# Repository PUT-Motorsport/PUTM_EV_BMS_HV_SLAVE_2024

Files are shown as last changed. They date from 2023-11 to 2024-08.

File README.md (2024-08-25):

# PUTM_EV_BMS_HV_SLAVE_2024
Accumulator Managment System (High Voltage Battery Managment System)

## Overview
The AMS system consists of two main parts, the master and multiple slaves.
<p align="center">
  
</p>
The apparatus is responsible for the managment of the battery as a whole, determining it's states like: state of charge or unsafe state plausibility. It also supervises the turning on and off of the hv bus.

## Slave
The AMS Slave is a subsidiary system responsible for measuring all the cell voltages and strategically placed temperatures on one stack.
<p align="center"> 
  
</p>

### Hardware 
The AMS Slave is powered by LTC6811, a powerful, new gen IC capable of measuring of up to 12 cell simultaneously and up to 5 auxilary readings. One slave features 2 of such IC for a total of 20 cell and 10 temperature measurements. All Slaves are connected in chain configuration allowing for a quick data dump from all slaves in series. For interfacing the LTC6811 uses isoSPI, a special SPI/Ethernet like protocol, which features amazing noise immunity due to usage of a twisted differential pair. All of that on a custom 4 layer board. The AMS slave boasts a lot smaller (106mm x 50mm) size compared to it's predecessor allowing for a lot more versatile usage and making one cell stack far more compact. 

<p align="center"> 
  
</p>

### The research and development work was carried out was a part of the Student Scientific Clubs Create Innovations (SKNTI) program. [Ministry of Science and Higher Education](https://www.gov.pl/web/nauka)
baner-sknti

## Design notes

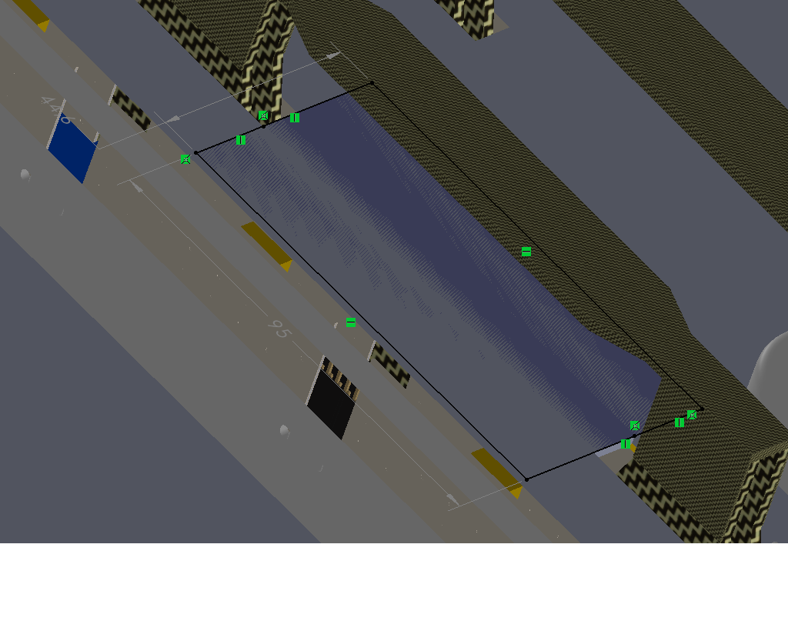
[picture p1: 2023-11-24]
hardware/images/wymiary v1.png

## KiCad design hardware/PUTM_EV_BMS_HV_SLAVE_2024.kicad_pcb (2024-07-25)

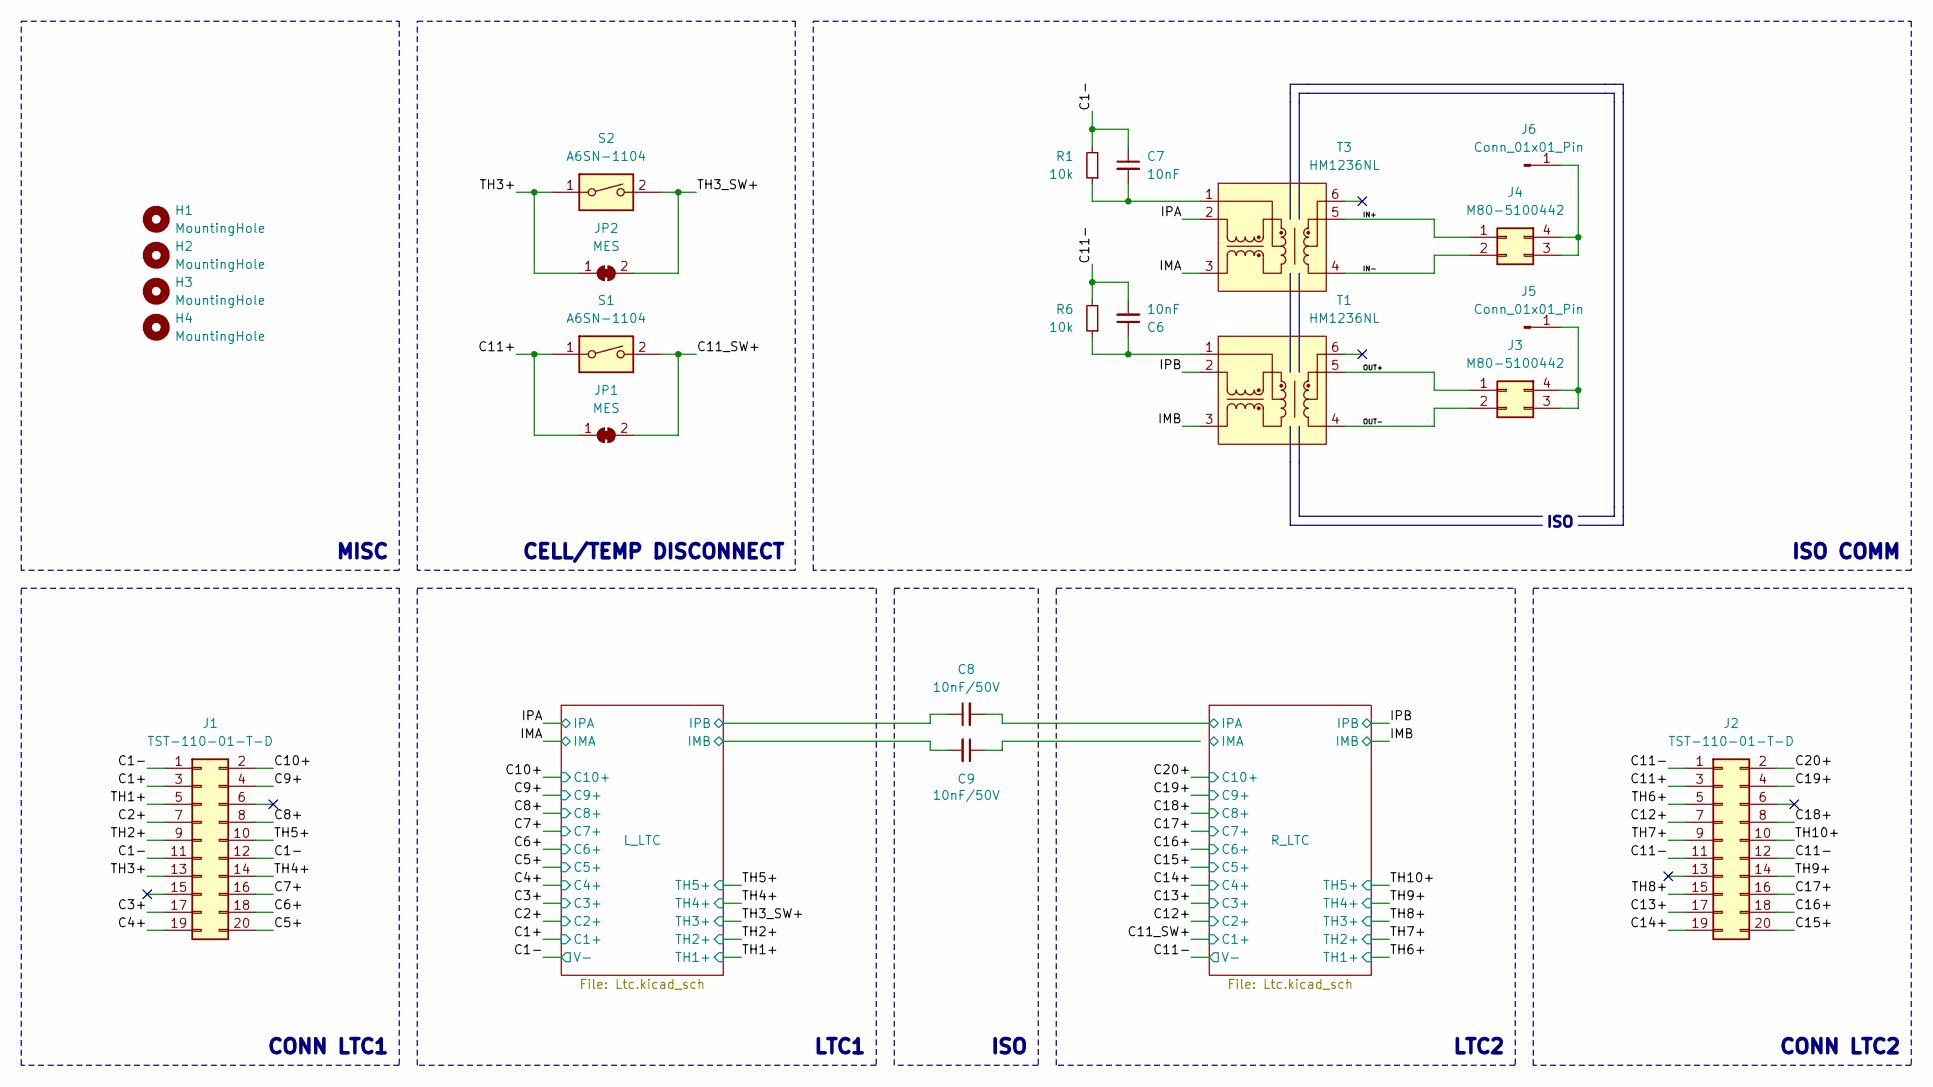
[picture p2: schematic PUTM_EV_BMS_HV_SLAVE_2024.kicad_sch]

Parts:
C6, C7: 10nF; C_0603_1608Metric; Manufacturer_Part_Number C0603C103J5RACTU; Mouser Part Number 80-C0603C103J5R
C8, C9: 10nF/50V; C_0603_1608Metric; Manufacturer_Part_Number C0603C104K4RAC7867; Mouser Part Number 80-C0603C104K4R7867
H1, H2, H3, H4: MountingHole; MountingHole_3.2mm_M3; Manufacturer_Part_Number --
J1, J2: TST-110-01-T-D; IDC-Header_2x10_P2.54mm_Vertical; Manufacturer_Part_Number TST-110-01-T-D; Mouser Part Number 200-TST11001TD
J3, J4: M80-5100442; M80-51004YY; Mouser Part Number 855-M80-5100442
J5, J6: Conn_01x01_Pin; SolderWire-0.1sqmm_1x01_D0.4mm_OD1mm_Relief; Manufacturer_Part_Number --
JP1, JP2: MES; SolderJumper-2_P1.3mm_Bridged2Bar_RoundedPad1.0x1.5mm; Manufacturer_Part_Number --
R1, R6: 10k; R_0603_1608Metric
S1, S2: A6SN-1104; A6SN1104; Mouser Part Number 653-A6SN-1104
T1, T3: HM1236NL; Mouser Part Number 673-HM1236NL

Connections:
/C1+: J1.3; also elsewhere on the board
/C1-: C7.1, J1.1, J1.11, J1.12, R1.2; also elsewhere on the board
/C2+: J1.7; also elsewhere on the board
/C3+: J1.17; also elsewhere on the board
/C4+: J1.19; also elsewhere on the board
/C5+: J1.20; also elsewhere on the board
/C6+: J1.18; also elsewhere on the board
/C7+: J1.16; also elsewhere on the board
/C8+: J1.8; also elsewhere on the board
/C9+: J1.4; also elsewhere on the board
/C10+: J1.2; also elsewhere on the board
/C11+: J2.3, JP1.1 (A), S1.1
/C11-: C6.2, J2.1, J2.11, J2.12, R6.2; also elsewhere on the board
/C11_SW+: JP1.2 (B), S1.2; also elsewhere on the board
/C12+: J2.7; also elsewhere on the board
/C13+: J2.17; also elsewhere on the board
/C14+: J2.19; also elsewhere on the board
/C15+: J2.20; also elsewhere on the board
/C16+: J2.18; also elsewhere on the board
/C17+: J2.16; also elsewhere on the board
/C18+: J2.8; also elsewhere on the board
/C19+: J2.4; also elsewhere on the board
/C20+: J2.2; also elsewhere on the board
/IMA: T3.3; also elsewhere on the board
/IMB: T1.3; also elsewhere on the board
/IN+: J4.1, T3.5
/IN-: J4.2, T3.4
/IPA: T3.2; also elsewhere on the board
/IPB: T1.2; also elsewhere on the board
/L_LTC/IMB: C9.2; also elsewhere on the board
/L_LTC/IPB: C8.1; also elsewhere on the board
/OUT+: J3.1, T1.5
/OUT-: J3.2, T1.4
/R_LTC/IMA: C9.1; also elsewhere on the board
/R_LTC/IPA: C8.2; also elsewhere on the board
/TH1+: J1.5; also elsewhere on the board
/TH2+: J1.9; also elsewhere on the board
/TH3+: J1.13, JP2.1 (A), S2.1
/TH3_SW+: JP2.2 (B), S2.2; also elsewhere on the board
/TH4+: J1.14; also elsewhere on the board
/TH5+: J1.10; also elsewhere on the board
/TH6+: J2.5; also elsewhere on the board
/TH7+: J2.9; also elsewhere on the board
/TH8+: J2.15; also elsewhere on the board
/TH9+: J2.14; also elsewhere on the board
/TH10+: J2.10; also elsewhere on the board
unnamed: C6.1, R6.1, T1.1
unnamed: C7.2, R1.1, T3.1
unnamed: J3.3, J3.4, J5.1
unnamed: J4.3, J4.4, J6.1

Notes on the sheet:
CELL/TEMP DISCONNECT
LTC1
MISC
ISO
CONN LTC1
ISO COMM
CONN LTC2
LTC2

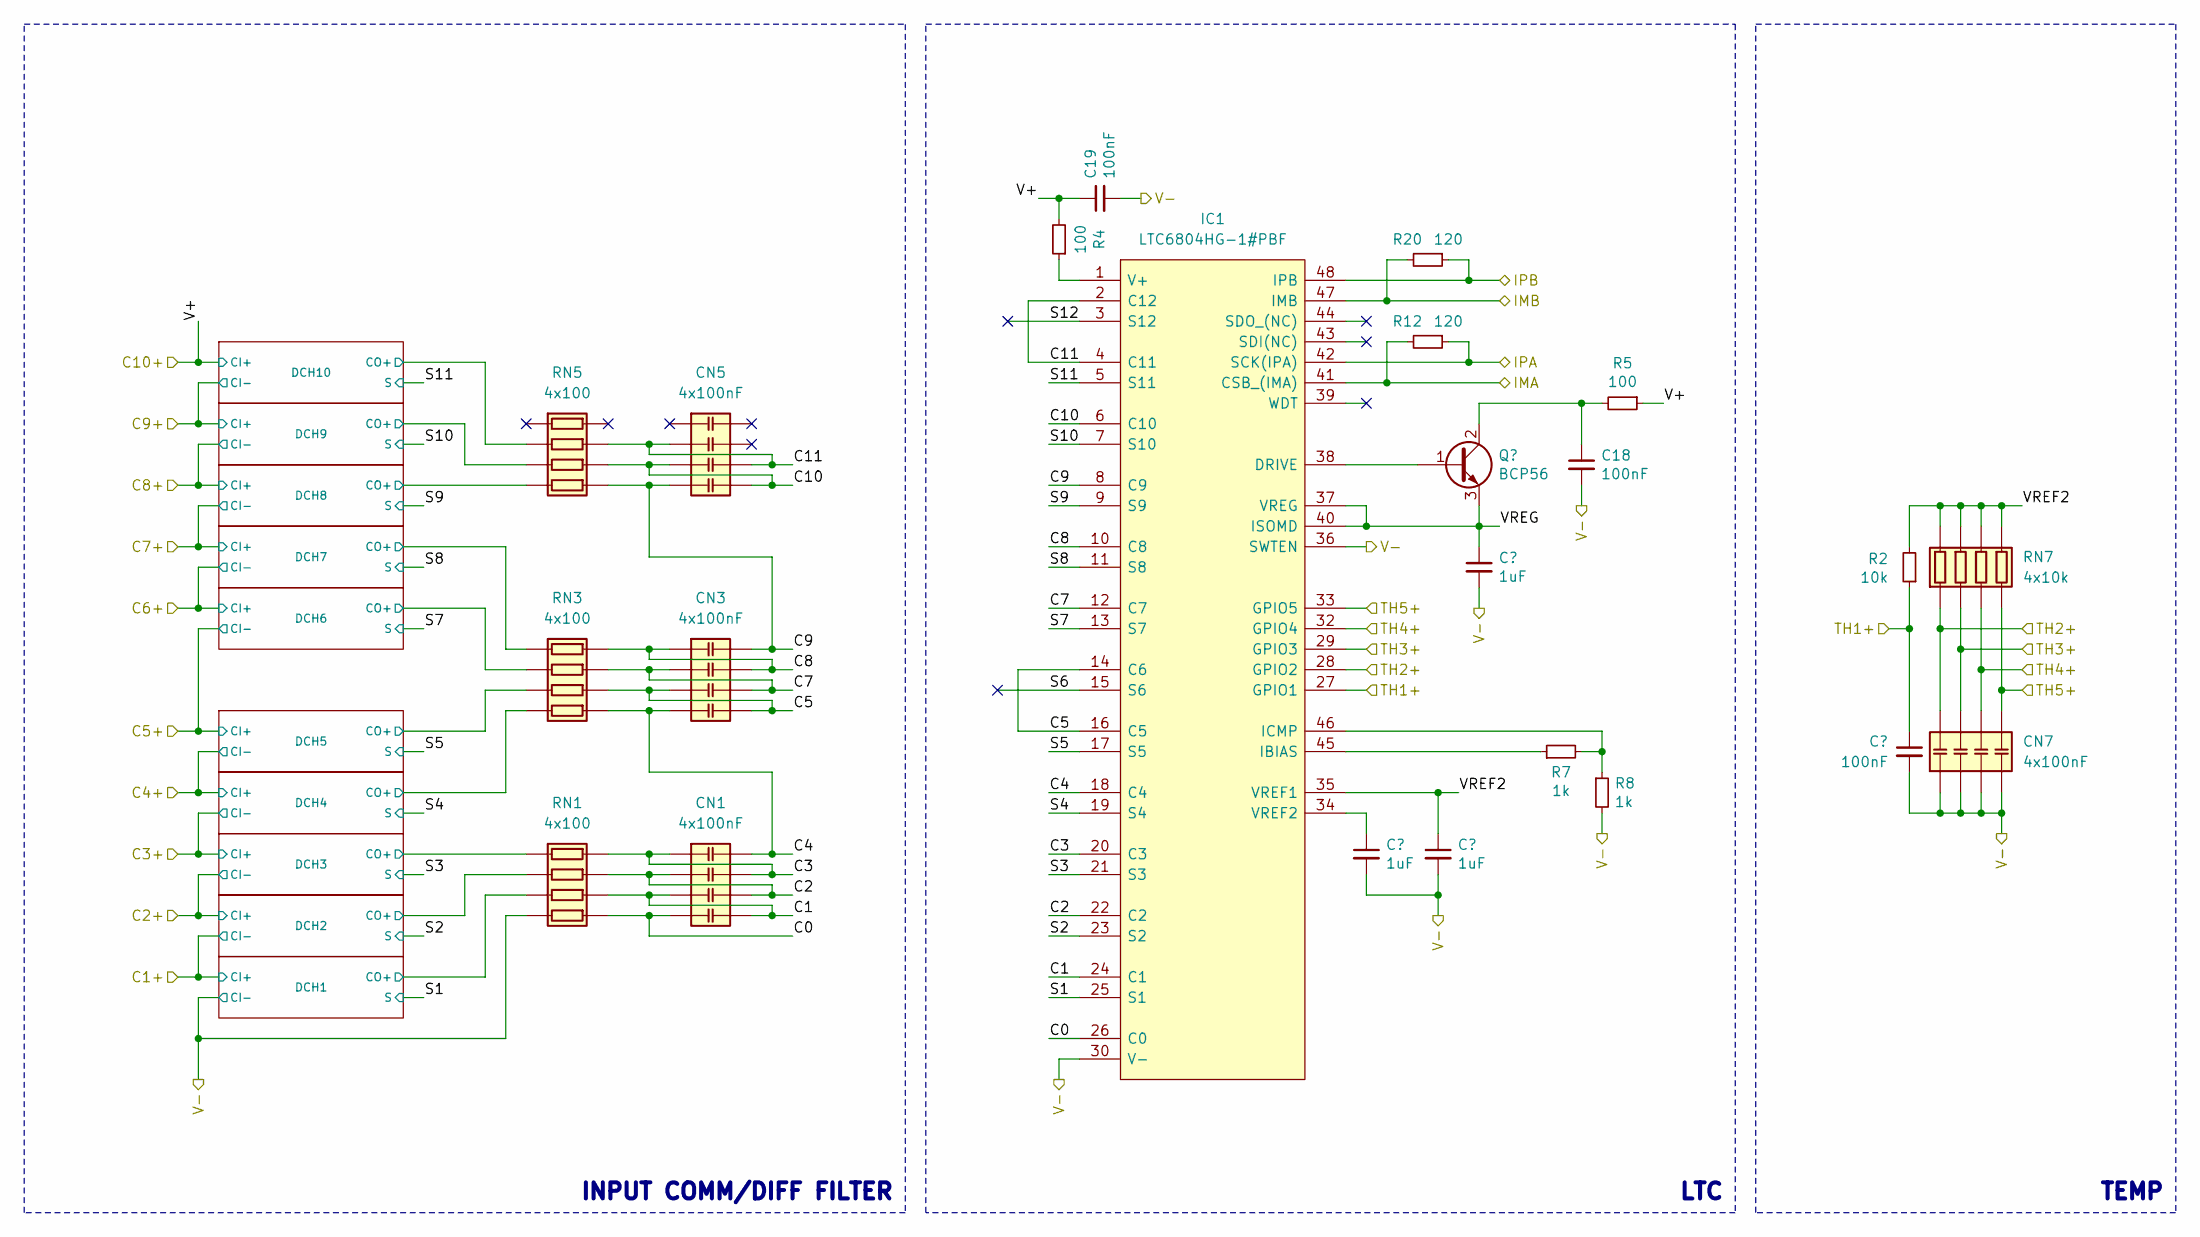
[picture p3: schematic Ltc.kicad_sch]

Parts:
C18, C19, C65: 100nF; C_0603_1608Metric; Manufacturer_Part_Number C0603C104K4RAC7867; Mouser Part Number 80-C0603C104K4R7867
CN1, CN3, CN5, CN7: 4x100nF; CA064X104K4RACAUTO; Mouser Part Number 80-CA064X104K4RCAUTO
IC1: LTC6804HG-1#PBF; SOP50P780X200-48N; Mouser Part Number 584-LTC6804HG-1#PBF
Q30: BCP56; SOT-223-3_TabPin2; Manufacturer_Part_Number BCP5616QTA; Mouser Part Number 621-BCP5616QTA
R2: 10k; R_0603_1608Metric; Manufacturer_Part_Number --
R4, R5: 100; R_0603_1608Metric; Manufacturer_Part_Number --
R7, R8: 1k; R_0603_1608Metric; Manufacturer_Part_Number --
R12, R20: 120; R_0603_1608Metric; Manufacturer_Part_Number --
RN1, RN3, RN5: 4x100; EXBV8V101JV; Mouser Part Number 667-EXB-V8V101JV
RN7: 4x10k; EXBV8V101JV; Mouser Part Number 667-EXB-V8V103GV

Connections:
/C1+: RN1.3 (R3.1); also elsewhere on the board
/C1-: C18.2, C19.2, CN7.1 (R1.1), CN7.2 (R2.1), CN7.3 (R3.1), CN7.4 (R4.1), IC1.30 (V-), IC1.31 (V-), IC1.36 (SWTEN), R8.2, RN1.4 (R4.1); also elsewhere on the board
/C2+: RN1.2 (R2.1); also elsewhere on the board
/C3+: RN1.1 (R1.1); also elsewhere on the board
/C4+: RN3.4 (R4.1); also elsewhere on the board
/C5+: RN3.3 (R3.1); also elsewhere on the board
/C6+: RN3.2 (R2.1); also elsewhere on the board
/C7+: RN3.1 (R1.1); also elsewhere on the board
/C8+: RN5.4 (R4.1); also elsewhere on the board
/C9+: RN5.3 (R3.1); also elsewhere on the board
/C10+: C19.1, R4.2, R5.1, RN5.2 (R2.1); also elsewhere on the board
/IMA: IC1.41 (CSB_(IMA)), R12.2; also elsewhere on the board
/IPA: IC1.42 (SCK(IPA)), R12.1; also elsewhere on the board
/L_LTC/C0: CN1.4 (R4.1), IC1.26 (C0), RN1.5 (R4.2)
/L_LTC/C1: CN1.3 (R3.1), CN1.5 (R4.2), IC1.24 (C1), RN1.6 (R3.2)
/L_LTC/C2: CN1.2 (R2.1), CN1.6 (R3.2), IC1.22 (C2), RN1.7 (R2.2)
/L_LTC/C3: CN1.1 (R1.1), CN1.7 (R2.2), IC1.20 (C3), RN1.8 (R1.2)
/L_LTC/C4: CN1.8 (R1.2), CN3.4 (R4.1), IC1.18 (C4), RN3.5 (R4.2)
/L_LTC/C5: CN3.3 (R3.1), CN3.5 (R4.2), IC1.14 (C6), IC1.16 (C5), RN3.6 (R3.2)
/L_LTC/C7: CN3.2 (R2.1), CN3.6 (R3.2), IC1.12 (C7), RN3.7 (R2.2)
/L_LTC/C8: CN3.1 (R1.1), CN3.7 (R2.2), IC1.10 (C8), RN3.8 (R1.2)
/L_LTC/C9: CN3.8 (R1.2), CN5.4 (R4.1), IC1.8 (C9), RN5.5 (R4.2)
/L_LTC/C10: CN5.3 (R3.1), CN5.5 (R4.2), IC1.6 (C10), RN5.6 (R3.2)
/L_LTC/C11: CN5.2 (R2.1), CN5.6 (R3.2), IC1.2 (C12), IC1.4 (C11), RN5.7 (R2.2)
/L_LTC/IMB: IC1.47 (IMB), R20.2; also elsewhere on the board
/L_LTC/IPB: IC1.48 (IPB), R20.1; also elsewhere on the board
/L_LTC/S1: IC1.25 (S1); also elsewhere on the board
/L_LTC/S2: IC1.23 (S2); also elsewhere on the board
/L_LTC/S3: IC1.21 (S3); also elsewhere on the board
/L_LTC/S4: IC1.19 (S4); also elsewhere on the board
/L_LTC/S5: IC1.17 (S5); also elsewhere on the board
/L_LTC/S6: IC1.15 (S6)
/L_LTC/S7: IC1.13 (S7); also elsewhere on the board
/L_LTC/S8: IC1.11 (S8); also elsewhere on the board
/L_LTC/S9: IC1.9 (S9); also elsewhere on the board
/L_LTC/S10: IC1.7 (S10); also elsewhere on the board
/L_LTC/S11: IC1.5 (S11); also elsewhere on the board
/L_LTC/S12: IC1.3 (S12)
/L_LTC/VREF2: IC1.35 (VREF1), R2.2, RN7.5 (R4.2), RN7.6 (R3.2), RN7.7 (R2.2), RN7.8 (R1.2); also elsewhere on the board
/L_LTC/VREG: IC1.37 (VREG), IC1.40 (ISOMD); also elsewhere on the board
/TH1+: IC1.27 (GPIO1), R2.1; also elsewhere on the board
/TH2+: CN7.8 (R1.2), IC1.28 (GPIO2), RN7.1 (R1.1); also elsewhere on the board
/TH3_SW+: CN7.7 (R2.2), IC1.29 (GPIO3), RN7.2 (R2.1); also elsewhere on the board
/TH4+: CN7.6 (R3.2), IC1.32 (GPIO4), RN7.3 (R3.1); also elsewhere on the board
/TH5+: CN7.5 (R4.2), IC1.33 (GPIO5), RN7.4 (R4.1); also elsewhere on the board
unnamed 138: IC1.38 (DRIVE); also elsewhere on the board
unnamed: IC1.45 (IBIAS), R7.1
unnamed: IC1.46 (ICMP), R7.2, R8.1
unnamed: IC1.1 (V+), R4.1
unnamed 142: IC1.34 (VREF2); also elsewhere on the board
unnamed 150: C18.1, R5.2; also elsewhere on the board

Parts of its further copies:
C4, C5, C20, C24: 100nF; C_0603_1608Metric; Manufacturer_Part_Number C0603C104K4RAC7867; Mouser Part Number 80-C0603C104K4R7867
CN2, CN4, CN6, CN8: 4x100nF; CA064X104K4RACAUTO; Mouser Part Number 80-CA064X104K4RCAUTO
IC2: LTC6804HG-1#PBF; SOP50P780X200-48N; Mouser Part Number 584-LTC6804HG-1#PBF
Q1, Q12: BCP56; SOT-223-3_TabPin2; Manufacturer_Part_Number BCP5616QTA; Mouser Part Number 621-BCP5616QTA
R3: 10k; R_0603_1608Metric; Manufacturer_Part_Number --
R28, R32: 120; R_0603_1608Metric; Manufacturer_Part_Number --
R51, R53: 100; R_0603_1608Metric; Manufacturer_Part_Number --
R52, R54: 1k; R_0603_1608Metric; Manufacturer_Part_Number --
RN2, RN4, RN6: 4x100; EXBV8V101JV; Mouser Part Number 667-EXB-V8V101JV
RN8: 4x10k; EXBV8V101JV; Mouser Part Number 667-EXB-V8V103GV

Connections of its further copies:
/C1-: C4.2; also elsewhere on the board
/C11-: C5.2, C20.2, C24.2, CN8.1 (R1.1), CN8.2 (R2.1), CN8.3 (R3.1), CN8.4 (R4.1), IC2.30 (V-), IC2.31 (V-), IC2.36 (SWTEN), R54.2, RN2.4 (R4.1); also elsewhere on the board
/C11_SW+: RN2.3 (R3.1); also elsewhere on the board
/C12+: RN2.2 (R2.1); also elsewhere on the board
/C13+: RN2.1 (R1.1); also elsewhere on the board
/C14+: RN4.4 (R4.1); also elsewhere on the board
/C15+: RN4.3 (R3.1); also elsewhere on the board
/C16+: RN4.2 (R2.1); also elsewhere on the board
/C17+: RN4.1 (R1.1); also elsewhere on the board
/C18+: RN6.4 (R4.1); also elsewhere on the board
/C19+: RN6.3 (R3.1); also elsewhere on the board
/C20+: C20.1, R51.2, R53.1, RN6.2 (R2.1); also elsewhere on the board
/IMB: IC2.47 (IMB), R32.2; also elsewhere on the board
/IPB: IC2.48 (IPB), R32.1; also elsewhere on the board
/L_LTC/VREG: Q1.3 (E); also elsewhere on the board
/R_LTC/C0: CN2.4 (R4.1), IC2.26 (C0), RN2.5 (R4.2)
/R_LTC/C1: CN2.3 (R3.1), CN2.5 (R4.2), IC2.24 (C1), RN2.6 (R3.2)
/R_LTC/C2: CN2.2 (R2.1), CN2.6 (R3.2), IC2.22 (C2), RN2.7 (R2.2)
/R_LTC/C3: CN2.1 (R1.1), CN2.7 (R2.2), IC2.20 (C3), RN2.8 (R1.2)
/R_LTC/C4: CN2.8 (R1.2), CN4.4 (R4.1), IC2.18 (C4), RN4.5 (R4.2)
/R_LTC/C5: CN4.3 (R3.1), CN4.5 (R4.2), IC2.14 (C6), IC2.16 (C5), RN4.6 (R3.2)
/R_LTC/C7: CN4.2 (R2.1), CN4.6 (R3.2), IC2.12 (C7), RN4.7 (R2.2)
/R_LTC/C8: CN4.1 (R1.1), CN4.7 (R2.2), IC2.10 (C8), RN4.8 (R1.2)
/R_LTC/C9: CN4.8 (R1.2), CN6.4 (R4.1), IC2.8 (C9), RN6.5 (R4.2)
/R_LTC/C10: CN6.3 (R3.1), CN6.5 (R4.2), IC2.6 (C10), RN6.6 (R3.2)
/R_LTC/C11: CN6.2 (R2.1), CN6.6 (R3.2), IC2.2 (C12), IC2.4 (C11), RN6.7 (R2.2)
/R_LTC/IMA: IC2.41 (CSB_(IMA)), R28.2; also elsewhere on the board
/R_LTC/IPA: IC2.42 (SCK(IPA)), R28.1; also elsewhere on the board
/R_LTC/S1: IC2.25 (S1); also elsewhere on the board
/R_LTC/S2: IC2.23 (S2); also elsewhere on the board
/R_LTC/S3: IC2.21 (S3); also elsewhere on the board
/R_LTC/S4: IC2.19 (S4); also elsewhere on the board
/R_LTC/S5: IC2.17 (S5); also elsewhere on the board
/R_LTC/S6: IC2.15 (S6)
/R_LTC/S7: IC2.13 (S7); also elsewhere on the board
/R_LTC/S8: IC2.11 (S8); also elsewhere on the board
/R_LTC/S9: IC2.9 (S9); also elsewhere on the board
/R_LTC/S10: IC2.7 (S10); also elsewhere on the board
/R_LTC/S11: IC2.5 (S11); also elsewhere on the board
/R_LTC/S12: IC2.3 (S12)
/R_LTC/VREF2: IC2.35 (VREF1), R3.2, RN8.5 (R4.2), RN8.6 (R3.2), RN8.7 (R2.2), RN8.8 (R1.2); also elsewhere on the board
/R_LTC/VREG: IC2.37 (VREG), IC2.40 (ISOMD), Q12.3 (E); also elsewhere on the board
/TH1+: C4.1; also elsewhere on the board
/TH6+: C5.1, IC2.27 (GPIO1), R3.1; also elsewhere on the board
/TH7+: CN8.8 (R1.2), IC2.28 (GPIO2), RN8.1 (R1.1); also elsewhere on the board
/TH8+: CN8.7 (R2.2), IC2.29 (GPIO3), RN8.2 (R2.1); also elsewhere on the board
/TH9+: CN8.6 (R3.2), IC2.32 (GPIO4), RN8.3 (R3.1); also elsewhere on the board
/TH10+: CN8.5 (R4.2), IC2.33 (GPIO5), RN8.4 (R4.1); also elsewhere on the board
unnamed 138: Q1.1 (B); also elsewhere on the board
unnamed: IC2.38 (DRIVE), Q12.1 (B)
unnamed: IC2.45 (IBIAS), R52.1
unnamed: IC2.46 (ICMP), R52.2, R54.1
unnamed: IC2.1 (V+), R51.1
unnamed 147: IC2.34 (VREF2); also elsewhere on the board
unnamed 150: Q1.2 (C); also elsewhere on the board
unnamed: C24.1, Q12.2 (C), R53.2

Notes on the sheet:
TEMP
LTC
INPUT COMM/DIFF FILTER

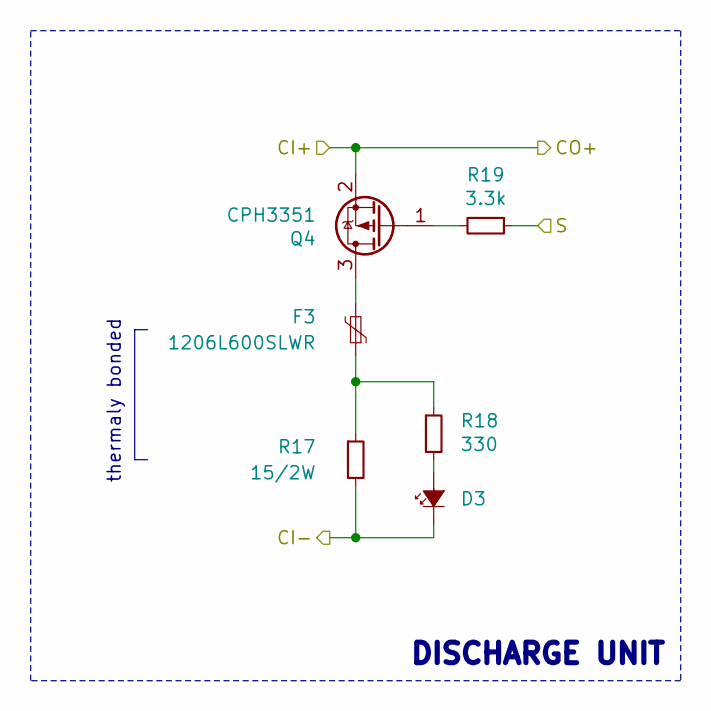
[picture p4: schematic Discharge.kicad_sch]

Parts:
D3: LED; LED_0603_1608Metric; Manufacturer_Part_Number 150060SS75000; Mouser Part Number 710-150060SS75000
F3: 1206L600SLWR; 1206L075SLYR; Mouser Part Number 576-1206L600SLWR
Q4: CPH3351; SOT-23; Manufacturer_Part_Number MMFTP3401; Mouser Part Number 637-MMFTP3401
R17: 15/2W; RESC6331X80N; Manufacturer_Part_Number CRM2512QFW-10R0ELF; Mouser Part Number 652-CRM2512QFW-10R0E
R18: 330; R_0603_1608Metric; Manufacturer_Part_Number RT0603FRE07330RL; Mouser Part Number 603-RT0603FRE07330RL
R19: 3.3k; R_0603_1608Metric; Manufacturer_Part_Number RT0603FRE073K3L; Mouser Part Number 603-RT0603FRE073K3L

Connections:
/C2+: D3.1 (K), R17.2; also elsewhere on the board
/C3+: Q4.2 (S); also elsewhere on the board
/L_LTC/S3: R19.1; also elsewhere on the board
unnamed: D3.2 (A), R18.2
unnamed: F3.1, R17.1, R18.1
unnamed: F3.2, Q4.3 (D)
unnamed: Q4.1 (G), R19.2

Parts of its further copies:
D1, D2, D4, D5, D6, D7, D8, D9, D10, D11, D12, D13, D14, D15, D16, D17, D18, D19, D20: LED; LED_0603_1608Metric; Manufacturer_Part_Number 150060SS75000; Mouser Part Number 710-150060SS75000
F1, F2, F4, F5, F6, F7, F8, F9, F10, F11, F12, F13, F14, F15, F16, F17, F18, F19, F20: 1206L600SLWR; 1206L075SLYR; Mouser Part Number 576-1206L600SLWR
Q2, Q3, Q5, Q6, Q7, Q8, Q9, Q10, Q11, Q13, Q14, Q15, Q16, Q17, Q18, Q19, Q20, Q21, Q22: CPH3351; SOT-23; Manufacturer_Part_Number MMFTP3401; Mouser Part Number 637-MMFTP3401
R9, R13, R21, R25, R29, R33, R37, R41, R45, R59, R63, R67, R71, R75, R79, R83, R87, R91, R95: 15/2W; RESC6331X80N; Manufacturer_Part_Number CRM2512QFW-10R0ELF; Mouser Part Number 652-CRM2512QFW-10R0E
R10, R14, R22, R26, R30, R34, R38, R42, R46, R60, R64, R68, R72, R76, R80, R84, R88, R92, R96: 330; R_0603_1608Metric; Manufacturer_Part_Number RT0603FRE07330RL; Mouser Part Number 603-RT0603FRE07330RL
R11, R15, R23, R27, R31, R35, R39, R43, R47, R61, R65, R69, R73, R77, R81, R85, R89, R93, R97: 3.3k; R_0603_1608Metric; Manufacturer_Part_Number RT0603FRE073K3L; Mouser Part Number 603-RT0603FRE073K3L

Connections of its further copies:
/C1+: D2.1 (K), Q2.2 (S), R13.2; also elsewhere on the board
/C1-: D1.1 (K), R9.2; also elsewhere on the board
/C2+: Q3.2 (S); also elsewhere on the board
/C3+: D4.1 (K), R21.2; also elsewhere on the board
/C4+: D5.1 (K), Q5.2 (S), R25.2; also elsewhere on the board
/C5+: D6.1 (K), Q6.2 (S), R29.2; also elsewhere on the board
/C6+: D7.1 (K), Q7.2 (S), R33.2; also elsewhere on the board
/C7+: D8.1 (K), Q8.2 (S), R37.2; also elsewhere on the board
/C8+: D9.1 (K), Q9.2 (S), R41.2; also elsewhere on the board
/C9+: D10.1 (K), Q10.2 (S), R45.2; also elsewhere on the board
/C10+: Q11.2 (S); also elsewhere on the board
/C11-: D14.1 (K), R71.2; also elsewhere on the board
/C11_SW+: D17.1 (K), Q16.2 (S), R83.2; also elsewhere on the board
/C12+: D16.1 (K), Q19.2 (S), R79.2; also elsewhere on the board
/C13+: D18.1 (K), Q18.2 (S), R87.2; also elsewhere on the board
/C14+: D11.1 (K), Q20.2 (S), R59.2; also elsewhere on the board
/C15+: D15.1 (K), Q13.2 (S), R75.2; also elsewhere on the board
/C16+: D20.1 (K), Q17.2 (S), R95.2; also elsewhere on the board
/C17+: D19.1 (K), Q22.2 (S), R91.2; also elsewhere on the board
/C18+: D12.1 (K), Q21.2 (S), R63.2; also elsewhere on the board
/C19+: D13.1 (K), Q14.2 (S), R67.2; also elsewhere on the board
/C20+: Q15.2 (S); also elsewhere on the board
/L_LTC/S1: R11.1; also elsewhere on the board
/L_LTC/S2: R15.1; also elsewhere on the board
/L_LTC/S4: R23.1; also elsewhere on the board
/L_LTC/S5: R27.1; also elsewhere on the board
/L_LTC/S7: R31.1; also elsewhere on the board
/L_LTC/S8: R35.1; also elsewhere on the board
/L_LTC/S9: R39.1; also elsewhere on the board
/L_LTC/S10: R43.1; also elsewhere on the board
/L_LTC/S11: R47.1; also elsewhere on the board
/R_LTC/S1: R73.1; also elsewhere on the board
/R_LTC/S2: R85.1; also elsewhere on the board
/R_LTC/S3: R81.1; also elsewhere on the board
/R_LTC/S4: R89.1; also elsewhere on the board
/R_LTC/S5: R61.1; also elsewhere on the board
/R_LTC/S7: R77.1; also elsewhere on the board
/R_LTC/S8: R97.1; also elsewhere on the board
/R_LTC/S9: R93.1; also elsewhere on the board
/R_LTC/S10: R65.1; also elsewhere on the board
/R_LTC/S11: R69.1; also elsewhere on the board
unnamed: D1.2 (A), R10.2
unnamed: D2.2 (A), R14.2
unnamed: D4.2 (A), R22.2
unnamed: D5.2 (A), R26.2
unnamed: D6.2 (A), R30.2
unnamed: D7.2 (A), R34.2
unnamed: D8.2 (A), R38.2
unnamed: D9.2 (A), R42.2
unnamed: D10.2 (A), R46.2
unnamed: D11.2 (A), R60.2
unnamed: D12.2 (A), R64.2
unnamed: D13.2 (A), R68.2
unnamed: D14.2 (A), R72.2
unnamed: D15.2 (A), R76.2
unnamed: D16.2 (A), R80.2
unnamed: D17.2 (A), R84.2
unnamed: D18.2 (A), R88.2
unnamed: D19.2 (A), R92.2
unnamed: D20.2 (A), R96.2
unnamed: F1.1, R9.1, R10.1
unnamed: F2.1, R13.1, R14.1
unnamed: F4.1, R21.1, R22.1
unnamed: F5.1, R25.1, R26.1
unnamed: F6.1, R29.1, R30.1
unnamed: F7.1, R33.1, R34.1
unnamed: F8.1, R37.1, R38.1
unnamed: F9.1, R41.1, R42.1
unnamed: F10.1, R45.1, R46.1
unnamed: F11.1, R59.1, R60.1
unnamed: F12.1, R63.1, R64.1
unnamed: F13.1, R67.1, R68.1
unnamed: F14.1, R71.1, R72.1
unnamed: F15.1, R75.1, R76.1
unnamed: F16.1, R79.1, R80.1
unnamed: F17.1, R83.1, R84.1
unnamed: F18.1, R87.1, R88.1
unnamed: F19.1, R91.1, R92.1
unnamed: F20.1, R95.1, R96.1
unnamed: F1.2, Q2.3 (D)
unnamed: Q2.1 (G), R11.2
unnamed: F2.2, Q3.3 (D)
unnamed: Q3.1 (G), R15.2
unnamed: F4.2, Q5.3 (D)
unnamed: Q5.1 (G), R23.2
unnamed: F5.2, Q6.3 (D)
unnamed: Q6.1 (G), R27.2
unnamed: F6.2, Q7.3 (D)
unnamed: Q7.1 (G), R31.2
unnamed: F7.2, Q8.3 (D)
unnamed: Q8.1 (G), R35.2
unnamed: F8.2, Q9.3 (D)
unnamed: Q9.1 (G), R39.2
unnamed: F9.2, Q10.3 (D)
unnamed: Q10.1 (G), R43.2
unnamed: F10.2, Q11.3 (D)
unnamed: Q11.1 (G), R47.2
unnamed: F11.2, Q13.3 (D)
unnamed: Q13.1 (G), R61.2
unnamed: F12.2, Q14.3 (D)
unnamed: Q14.1 (G), R65.2
unnamed: F13.2, Q15.3 (D)
unnamed: Q15.1 (G), R69.2
unnamed: F14.2, Q16.3 (D)
unnamed: Q16.1 (G), R73.2
unnamed: F15.2, Q17.3 (D)
unnamed: Q17.1 (G), R77.2
unnamed: F16.2, Q18.3 (D)
unnamed: Q18.1 (G), R81.2
unnamed: F17.2, Q19.3 (D)
unnamed: Q19.1 (G), R85.2
unnamed: F18.2, Q20.3 (D)
unnamed: Q20.1 (G), R89.2
unnamed: F19.2, Q21.3 (D)
unnamed: Q21.1 (G), R93.2
unnamed: F20.2, Q22.3 (D)
unnamed: Q22.1 (G), R97.2

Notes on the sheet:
DISCHARGE UNIT
thermaly bonded

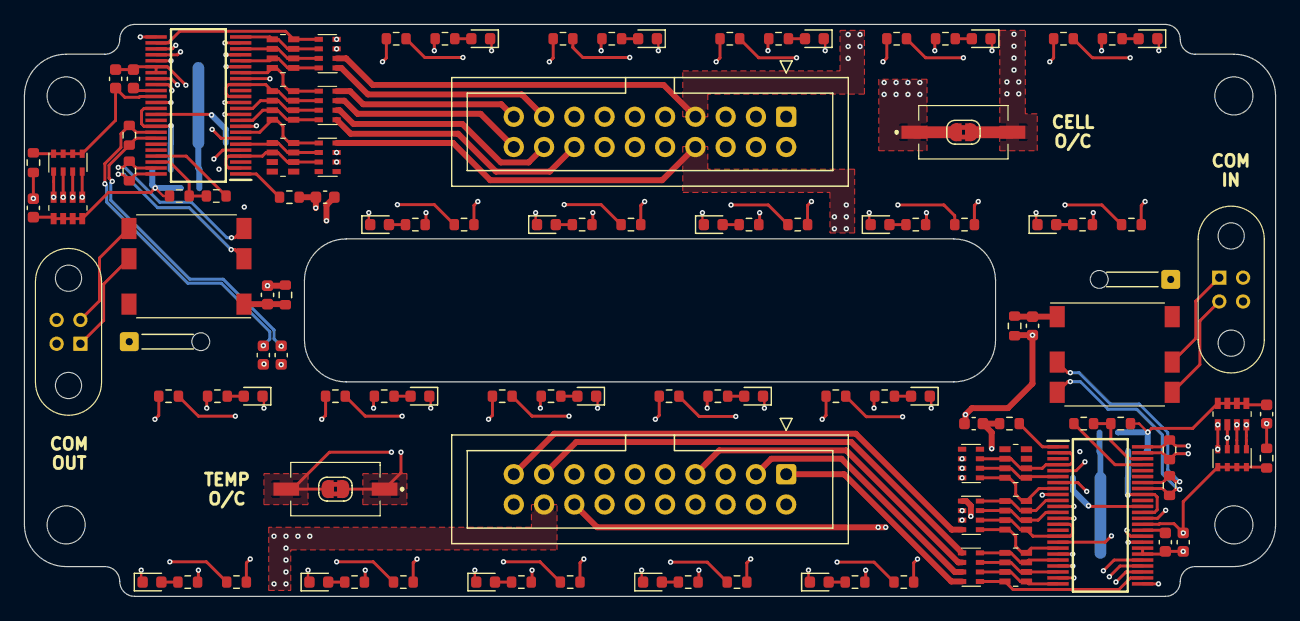
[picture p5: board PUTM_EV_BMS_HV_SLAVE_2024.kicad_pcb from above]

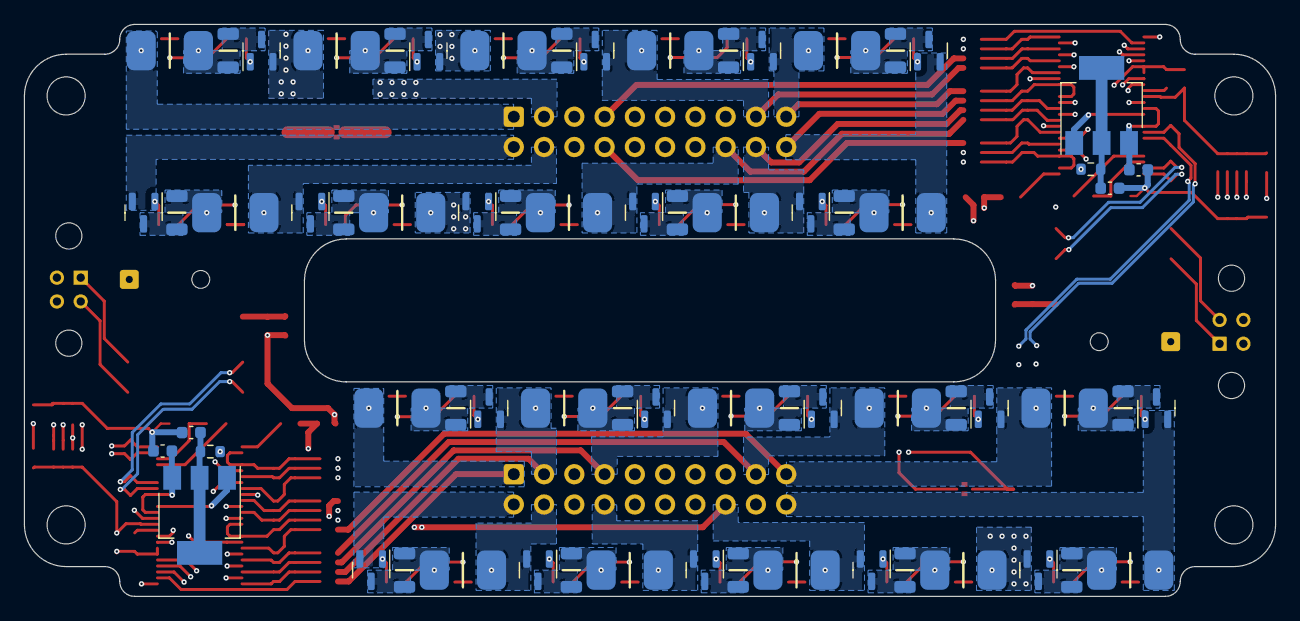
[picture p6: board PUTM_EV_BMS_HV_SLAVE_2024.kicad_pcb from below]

Board: 4 copper layers, 105.0 x 48.0 mm, 188 parts (68 on the bottom side), 188 nets.

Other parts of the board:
C1, C2, C3, C21, C22, C23: 1uF; C_0603_1608Metric

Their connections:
/C1-: C1.2, C2.2, C3.2; also elsewhere on the board
/C11-: C21.2, C22.2, C23.2; also elsewhere on the board
/L_LTC/VREF2: C2.1; also elsewhere on the board
/L_LTC/VREG: C3.1; also elsewhere on the board
/R_LTC/VREF2: C22.1; also elsewhere on the board
/R_LTC/VREG: C23.1; also elsewhere on the board
unnamed 142: C1.1; also elsewhere on the board
unnamed 147: C21.1; also elsewhere on the board

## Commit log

2023-10-30 v2.0.1 testing designs
    [Discharge.kicad_sch, Ltc.kicad_sch, PUTM_EV_BMS_HV_SLAVE_2024.kicad_pcb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]
2023-11-14 spaced out version
    [Discharge.kicad_sch, Ltc.kicad_sch, PUTM_EV_BMS_HV_SLAVE_2024.kicad_pcb]
2023-11-21 finished layout
    [Discharge.kicad_sch, Ltc.kicad_sch, PUTM_EV_BMS_HV_SLAVE_2024.kicad_pcb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]
2023-11-24 final version
    [PUTM_EV_BMS_HV_SLAVE_2024.kicad_pcb]
2024-06-03 change from transformator to capacitive isolation between ltc, change ibias/icmp pin since they are incorrectly connected
    [Discharge.kicad_sch, Ltc.kicad_sch, PUTM_EV_BMS_HV_SLAVE_2024.kicad_pcb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]
2024-07-15 new 1.2 revision
    [PUTM_EV_BMS_HV_SLAVE_2024.kicad_pcb, PUTM_EV_BMS_HV_SLAVE_2024.kicad_sch]
2024-07-25 added temp disconnect, beautify schematic
    [Discharge.kicad_sch, Ltc.kicad_sch, PUTM_EV_BMS_HV_SLAVE_2024.kicad_pcb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]
